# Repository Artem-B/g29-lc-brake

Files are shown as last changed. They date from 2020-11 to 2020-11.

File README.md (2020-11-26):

# Logitech G29 pedals mod
- [Logitech G29 pedals mod](#logitech-g29-pedals-mod)
  - [What it does](#what-it-does)
  - [Why](#why)
  - [Required hardware](#required-hardware)
  - [Software](#software)
  - [Hardware -- the real hardware this time.](#hardware----the-real-hardware-this-time)
- [Build instructions](#build-instructions)

## What it does

- Adds load cell as the brake pressure sensor.
  - replaces lower part of the spring housing with a 3D-printed one.
- Adds Adafruit ItsyBitsy M4 express to process load cell data and
  potentiomenter readings as an independent (from the wheel) HID joystick with
  16-bit values. Un-invert the values reported by pedals while we're at that.

## Why

Humans easily adapt to control car braking by applying **pressure**. Logitech
pedals use potentiomenters that read pedal displacement. Relationship between
the applied pressure and the displacemmment is controlled by the brake's spring
with a rubber block intended to make the relationship non-linear. Unfortunately,
it squeezes whe wide range of high pressure values at the end of the pedal
travel into a rather narrow range of the pedal movement which Logitech software then attempts to normalize into something more sensible.

It mostly works, but in practice I've found it rather hard to modulate the brake pressure precisely. One moment the car does not brake enough, then all of a sudden ABS goes nuts (or the car spins out). It just does not behave like a real car brake.

So, after eyeballing various higher-end pedals I've decided that I'm not *that*
interested in spending my toy budget on the ready-made gear. Instead, I've
figured that I can just mod the pedals using mostly off-the shelf components and
whatever I had at hand.

TL; DR; It worked surprisingly well. Eventually.

## Required hardware

- Logitech G29/G920 pedals. The mod may work with G27 or other similar Logitech
  models, but you may need to tweak the spring housing model to fit.

- $15 [Adafruit ItsyBitsy M4 Express](https://www.adafruit.com/product/3800)
  
  It's amazing how much stuff you can cram into $15 worth of hardware:
  - ATSAMD51 32-bit Cortex M4 core running at 120 MHz
   
    You get a real 32-bit ARM processor, with tons of peripherals and you can
    program it in Python, if you want to. Why anyone is still using AVR-based
    overpriced and underpowered Arduino boards these days is beyond me.
  - Floating point support with Cortex M4 DSP instructions. -- M4 can do *a lot*
    of signal processing, if needed.
  - 512 KB flash, 192 KB RAM -- should be enough for everyone, right?
  - 2 MB SPI FLASH chip for storing files and CircuitPython code storage.

  Another option is [Feather M4](https://www.adafruit.com/product/3857) ($23)
  which uses the same processor as the `ItsyBitsy M4`  and comes with some
  breadboard space which would be handy.

  You could also save few bucks and go for [QT
  Py](https://www.adafruit.com/product/4600) ($6),  [Trinket
  M0](https://www.adafruit.com/product/3500) ($9), or [ItsyBitsy
  M0](https://www.adafruit.com/product/3727) ($12). These boards use `Cortex-M0`
  and are slower than the `Cortex-M4` on the `ItsyBitsy M4`, but should still be
  more than sufficient to do the job.

  Other thoughts:

    About any chip with an USB interface, couple of GPIO pins for I2C and three
    ADC-capable inputs could do the job. `ItsyBitsy M4` is way overpowered for
    that and was largely chosen for convenience of writing software in Python.

    Surprisingly, not that many low-cost Cortex-M based boards have USB support.
    My usual go-to
    [`Discovery`](https://www.st.com/en/evaluation-tools/stm32-discovery-kits.html)
    and
    [`Nucleo`](https://www.st.com/en/evaluation-tools/stm32-nucleo-boards.html)
    boards from `STM` use USB for built-in STLink debugger and only pass through
    UART to the host.

    Trivia bit: $13 STM's
    [Nucleo-32](https://www.st.com/en/evaluation-tools/nucleo-g431kb.html) which
    is based on `stm32f431kb` uses `stm32f723` for the built-in ST-Link
    debugger. `F732` alone costs as much as the board and is much more capable
    than the `stm32f4` chip it debugs. How can one buy the whole board for less
    than the sum of the parts is a mystery to me. Can't complain though.

    ESP32 may be an interesting option for interfacing with the computer via
    Bluetooth, but that was considered to go beyond the `keep it simple`
    approach I was going for.

- $30 [FX29K0](https://www.te.com/usa-en/product-CAT-FSE0006.html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)
  100lbf/50kg load cell with I2C interface. 
  
  - Part number: FX29K0-100A-0100-L
  - [Datasheet](https://www.te.com/commerce/DocumentDelivery/DDEController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) for FX29 load cells.
  - [Datasheet](https://www.idt.com/us/en/document/dst/zsc31014-datasheet) for `zsc31014` which is the measurement controller inside the FX29 load cell.

  There are quite a few variants of the load cell. You need the one starting
  with `FX29K` or `FX29J`, and ending with `0100-L` pr `0500-N`. If you use
  `FX29K`/`FX29J` followed by a digit other than `0`, you will need to adjust
  the I2C address in the `code.py`.

  The cell costs about $30 and is available from the usual sources.
  - [Digikey](https://www.digikey.com/en/products/detail/te-connectivity-measurement-specialties/FX29K0-100A-0100-L/11205661)
  - [Mouser](https://www.mouser.com/ProductDetail/Measurement-Specialties/FX29K0-100A-0100-L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)
  - [Others, via octopart.com](https://octopart.com/search?q=FX29K0-100A-0100-L&currency=USD&specs=0)

- Female DB-9 connector.
  
  Used to read the stock potentiomenter values via the reguler DB-9 connector from the pedals that normally plugs into the wheel base.

  I've repurposed an old serial cable I had in my `junk that may be useful one day` bin.

## Software

- [CircuitPython](https://circuitpython.readthedocs.io/en/6.0.x/README.html)
  
  That turned out to be the easiest way to get things working. I've considered
  multiple alternatives, but this method ended up winning based on the `results
  delivered`/`annoyance caused` ratio.

  - My [repo with the modified CirquitPython](https://github.com/Artem-B/circuitpython)

    The only changes are to ass `PEDALS` USB HID device for `ItsyBitsy M4 Express` board. If you want to use a different board, you'll need to make similar changes for that board.

  - Pedals software (this repo)
    
    It's a simple python script that reads the values from `FX29` and the values
    of the stock potentiometers and reports them via USB. It also continually
    prints all the values over the serial port. It could be used to measure the
    relatinship between pedal displacement and the reported load. E.g. here is
    what my brake pedal reports depending on the spring setup: brake pedal load/displacement chart

    The result is roughly comparable to the much more expensive 
    [Heusinkveld Sim Pedals Ultimate](https://www.cranfieldsimulation.com/shop/sim-pedals-ultimate-heusinkveld/):
    

## Hardware -- the real hardware this time.

- Coins. I've used Euro 10c, [Danish 2
  kroner](https://en.wikipedia.org/wiki/Danish_krone) (yay for a center hole!)
  and an US 25c coins. You could probably use other coins, possibly filed down to
  size, or find appropriately sized washers.
- M4-0.7x20 screw + nut, but the size is not particularly critical, we just need
  a bump that will push on the load cell.

First mod version was prototyped using a bunch of schedule 40 PVC pipes and
couplers. It didn't quite work out. I had to build both upper and lower parts of
the spring housing. Making the parts telescoping into each other was hard to do
within the limited size choices and the constraints imposed by the pedal frame.
Without parts snugly fitting into each other, the spring buckles under the load
and the whole contraption flies apart. It turns out g29 pedal design uses a
number of subtle tricks to constrain spring housing motion to prevent spring
buckling. 

# Build instructions

See [Build.md](./Build.md) for the gory details.

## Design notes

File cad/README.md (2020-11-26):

# 3D-printable CAD model for the lower part of the spring housing.



This directory contains design file in `STEP` format and `STL` model for 3D printing.

You can poke at the model online:
- [Onshape](https://cad.onshape.com/documents/33ba29857d75f513ac8580a0/w/af6bbb602e60010e2369d8d1/e/88f17d0aba57d4f3874d157d).
- [Fusion360](https://a360.co/3l7wu99)

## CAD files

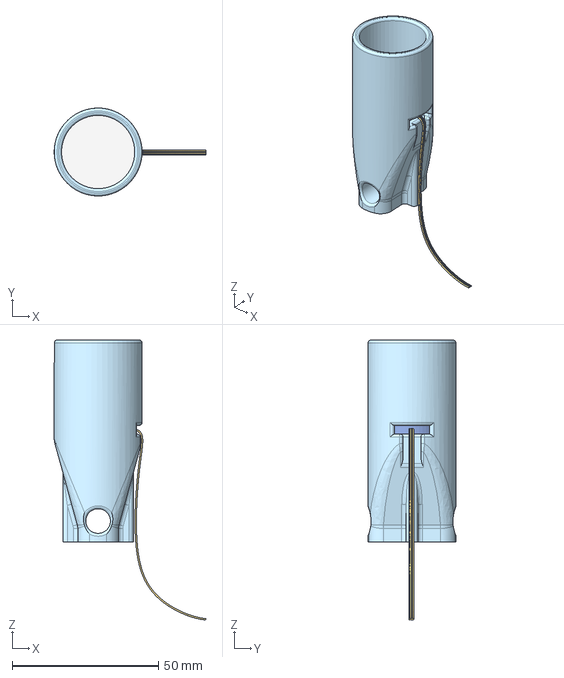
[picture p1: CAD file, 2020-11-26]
cad/g29 brake load cell mod.step
51.8 x 30.0 x 95.6 mm

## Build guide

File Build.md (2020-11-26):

# G29 brake mod build instructions.
- [G29 brake mod build instructions.](#g29-brake-mod-build-instructions)
  - [Software](#software)
    - [Build modified CircuitPython firmware](#build-modified-circuitpython-firmware)
    - [Update CircuitPython firmware](#update-circuitpython-firmware)
    - [Install required CircuitPython libraries](#install-required-circuitpython-libraries)
  - [Hardware](#hardware)
    - [Wiring](#wiring)
    - [3D print the spring holder](#3d-print-the-spring-holder)
    - [Assemble the mod](#assemble-the-mod)
    - [Mod the pedals.](#mod-the-pedals)
  - [Debugging](#debugging)

## Software

### Build modified CircuitPython firmware

Follow [CircuitPython build instructions](https://learn.adafruit.com/building-circuitpython/build-circuitpython) for `ItsyBitsy M4 Express`:

```shell
$ git clone https://github.com/Artem-B/circuitpython
$ cd circuitpython
$ git checkout main
$ git submodule sync --quiet --recursive
$ git submodule update --init
$ make -C mpy-cross
$ cd ports/atmel-samd
$ make BOARD=itsybitsy_m4_express
```

Once you're done you should have `build-itsybitsy_m4_express/firmware.uf2` file.

### Update CircuitPython firmware

Official Adafruit's [Firware upgrade instructions](https://learn.adafruit.com/introducing-adafruit-itsybitsy-m4/uf2-bootloader-details).

- double-click `reset` button on the ItsyBitsy board.
- you should see a new removable drive labeled `ITSYM4BOOT`
- copy `firmware.uf2` from the step above to that drive.

### Install required CircuitPython libraries

Once the firmware has been updated, you should see a new removable drive labeled
`CIRCUITPY`. That's where python files will go. 

- download the latest circuitpython library bundle from
  https://circuitpython.org/libraries and unpack it somewhere. Copy following
  files from the bundle into the `lib` directory on the `CIRCUITPY` drive:
  ```
  adafruit_hid/*
  simpleio.mpy
  ```
- copy all `.py` files from this repository into the root of the `CIRCUITPY` drive.

Software is ready to go now.

## Hardware

### Wiring

- I2C

    In order for I2C communication to work, you need to add two pull-up resistors -- one between `SCL` and `3.3V`, and one between `SDA` and `3.3V`.

- DB-9 for original pedal potentiomenters.

    Wire DB-9 Female connector pins to the following pins on `ItsyBitsy M4`:

    | DB-9 pin | `ItsyBitsy M4` pin | Purpose          |
    |----------|--------------------|------------------|
    |     1    | 3V                 | Reference voltage|
    |     2    | A0                 | Accelerometer pot|
    |     3    | A1                 | Brake pot        |
    |     4    | A2                 | Clutch pot       |
    |     6    | G                  | Signal Ground    |

- 4-pin connector for the load cell. 
  
  Wire connector pins for the load cell's signals:
    | load cell | `ItsyBitsy M4` pin |
    |-----------|--------------------|
    |  Red      | 3V. A5, if you want to change load cell parameters. |
    |  Yellow   | SCL                |
    |  White    | SDA                |
    |  Black    | G                  |

  I've used the standard 100mil header pins.

  The red wire supplies power to the load cell. In order to access the load
  cell's command mode, I2C command must be issued within 1.5-6ms of the cell power up. I've used a GPIO pin to supply the load cell's power. The cell's power consumption is below the 8mA that could be supplied by a GPIO pin on the `SAMD51G`. Powering the load cell from the 3.3V directly is fine for just reading the load cell measurements.

### 3D print the spring holder

3D print the model in [`CAD`](cad/README.md) subdirecory. I've printed it using
0.6mm nozzle and 0.4mm layer. You may need to file off the seams on the inside
and the outside of the printed part to ensure that the spring and the upper part
of the housing move smoothly.

### Assemble the mod

Attach the the washer to the bottom of the load cell using double-sided tape (it
must be about paper-thin, do not use thick foam tape) or some glue.

Thread the load cell cable through the hole in the side of the housing.

Place the load cell into the holder, with the load point bump facing upwards.

Drill a hole in a 25c coin, put a screw through it and fix it in position with a nut. The length of the screw should be short enough to fit under the white plastic cap in the original holder. Alternatively, you could place an appropriately sized stand-off on the screw and use that instead of the cap to guide/center the spring and serve as the support for the rubber insert, if you're planning to use one.

Place the coin & screw assembly into the housing, screw head down, so it contacts the load cell's center.

### Mod the pedals.

[Disassembly instructions](https://youtu.be/DxT2UOmHN-I?t=885) by `Sim Racing Garage` on YouTube.

- remove both parts of the spring housing.
- replace lower portion with the mod.
- Drill a hole in the upper part of the pedals' case and thread the load cell
  cable through.
- Drill two or four of holes on the back of the upper pedals shell and thread a
  zip-tie(s) through them. The zip ties will be used to mount the `ItsyBitsy M4`
  board.
- re-assemble the pedals.
- Connect the load call wires to the header you've soldered (or wire them to the
  `ItsyBitsy M4` directly)
- Plug in the original pedals connector to the female DB-9 you've wired above.
- Connect `ItsyBitsy M4` to the host via USB.

## Debugging

CircuitPython creates a virtual serial port. If/when something goes wrong, the normally-green LED on the `ItsyBitsy M4` will start flashing other colors. Connecting to the serial port will give you access to the Python REPL running on the board. When the mod app runs normally, it prints out every measured value for each of the potentiometers and for the load cell, so you can use it to verify that the pedals respond as intended.

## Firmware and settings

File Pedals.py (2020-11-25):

# The MIT License (MIT)
#
# Copyright (c) 2018 Dan Halbert for Adafruit Industries
#
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

"""
`adafruit_hid.gamepad.Gamepad`
====================================================
* Author(s): Dan Halbert
"""

import struct
import time

from adafruit_hid import find_device


class Pedals:
    """ """

    def __init__(self, devices):
        """Create a Gamepad object that will send USB gamepad HID reports.
        Devices can be a list of devices that includes a gamepad device or a gamepad device
        itself. A device is any object that implements ``send_report()``, ``usage_page`` and
        ``usage``.
        """
        self._device = find_device(devices, usage_page=0x1, usage=0x04)

        # Reuse this bytearray to send reports.
        # 4 reports, 2-byte each = 8 bytes.
        self._report = bytearray(8)

        # Remember the last report as well, so we can avoid sending
        # duplicate reports.
        self._last_report = bytearray(8)

        # Store settings separately before putting into report. Saves code
        # especially for buttons.
        self._joy_x = 0
        self._joy_y = 0
        self._joy_z = 0
        self._joy_w = 0

        # Send an initial report to test if HID device is ready.
        # If not, wait a bit and try once more.
        try:
            self.reset_all()
        except OSError:
            time.sleep(1)
            self.reset_all()

    def set(self, x=None, y=None, z=None, w=None):
        """Set and send the given joystick values.
        The joysticks will remain set with the given values until changed
        One joystick provides ``x`` and ``y`` values,
        and the other provides ``z`` and ``r_z`` (z rotation).
        Any values left as ``None`` will not be changed.
        All values must be in the range -127 to 127 inclusive.
        Examples::
            # Change x and y values only.
            gp.move_joysticks(x=100, y=-50)
            # Reset all joystick values to center position.
            gp.move_joysticks(0, 0, 0, 0)
        """
        if x is not None:
            self._joy_x = self._validate_value(x)
        if y is not None:
            self._joy_y = self._validate_value(y)
        if z is not None:
            self._joy_z = self._validate_value(z)
        if w is not None:
            self._joy_w = self._validate_value(w)
        self._send()

    def reset_all(self):
        """Release all buttons and set joysticks to zero."""
        self._joy_x = 0
        self._joy_y = 0
        self._joy_z = 0
        self._joy_w = 0
        self._send(always=True)

    def _send(self, always=False):
        """Send a report with all the existing settings.
        If ``always`` is ``False`` (the default), send only if there have been changes.
        """
        struct.pack_into(
            "<hhhh",
            self._report,
            0,
            self._joy_x,
            self._joy_y,
            self._joy_z,
            self._joy_w,
        )

        if always or self._last_report != self._report:
            self._device.send_report(self._report)
            # Remember what we sent, without allocating new storage.
            self._last_report[:] = self._report

    @staticmethod
    def _validate_value(value):
        if not -32768 <= value <= 32767:
            raise ValueError("Out of range")
        return value

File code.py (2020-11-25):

import board
import time
import simpleio
import usb_hid
import math
import digitalio
import analogio
from struct import pack_into, unpack
import Pedals

def f(x):
    return int(32760*math.sin(float(x)/1000.0))

pedals = Pedals.Pedals(usb_hid.devices)

def pedal_sim():
    t = 0;
    while True:
        print("t=", t)
        pedals.set(x=f(t), y=f(t*2), z=f(t*3), w=f(t*4))
        t = t+1
        time.sleep(0.01)

def scan_i2c():
    i2c = board.I2C()
    
    while not i2c.try_lock():
        pass
    
    try:
        while True:
            print("I2C addresses found:", [hex(device_address)
                for device_address in i2c.scan()])
            time.sleep(2)
    
    finally:  # unlock the i2c bus when ctrl-c'ing out of the loop
        i2c.unlock()    
        pass

class FX29:
    def __init__(self, addr=0x28, power_pin=board.A5):
        self._pwr = digitalio.DigitalInOut(power_pin)
        self._pwr.direction = digitalio.Direction.OUTPUT
        self.power(True)
        self._i2c = board.I2C()
        self._addr = addr
        self._buf = bytearray(4)
        self._i2c.unlock()
        while not self._i2c.try_lock():
            pass
        print("FX29 created")

    def power(self, on):
        self._pwr.value = on
        
    def read_mr(self):
        # Just read command & STOP
        self._i2c.readfrom_into(self._addr, self._buf, end = 0)

    @staticmethod
    def _sv(value):
        "Returns status/value tuple"
        s = value >> 14 & 0x3
        v = value & 0x3fff
        return s,v

    @staticmethod
    def _temp(value):
        "Returns temperature"
        t = value >> 5 & 0x3ff
        return t


    def read_mr2(self):
        # bridge data
        self._i2c.readfrom_into(self._addr, self._buf, end = 2)
        value, dummy = unpack('>HH', self._buf)
        s,v = self._sv(value)
        return s, v

    def read_mr4(self):
        # Bridge data & temperature
        self._i2c.readfrom_into(self._addr, self._buf)
        value, t = unpack('>HH', self._buf)
        s,v = self._sv(value)
        if s == 3:
            print("")
        return s, v, self._temp(t)


    def write_mr(self):
        # Write w/ no data
        self._i2c.writeto(self._addr, self._buf, end = 0)

    def enter_cmd_mode(self):
        self.power(False)
        time.sleep(0.01)
        self.power(True)
        time.sleep(0.003) # We have ~6 ms to enter command mode.
        self.cmd(0xA0)

    def exit_cmd_mode(self):
        self.cmd(0x80)
        time.sleep(0.02) # It may take up to 20ms to exit if we need to update EEPROM.
    
    def cmd(self, cmd, data=0):
        pack_into('>BHx', self._buf, 0, cmd, data)
        self._i2c.writeto(self._addr, self._buf, end=3)

    def read_eeprom(self, offset):
        if not 0 <= offset <= 0x13:
            return
        self.cmd(offset, 0)
        self._i2c.readfrom_into(self._addr, self._buf, end=3)
        ack, value = unpack('>BHx', self._buf)
        if ack != 0x5a:
            print("Got unexpected EEPROM read response:", hex(ack), hex(value))
            return
        return value

    def write_eeprom(self, offset, value):
        if not 0 <= offset <= 0x13:
            return
        v0 = self.read_eeprom(offset)
        # Write the new value
        self.cmd(0x40+offset, value)
        time.sleep(0.02) # EEPROM write takes up to 15ms
        v1 = self.read_eeprom(offset)
        print("W[%d]= %s:  %s -> %s" % (offset, hex(value), hex(v0), hex(v1)))

def adc_to_axis(v):
    return -32768 + (0xffff - v)

def load_to_axis(v):
    return int(-32768 + 3 * max(0, v-1000)) # Full span is 1000-15000, stretch it a bit.

def measure(fx29):
    accelerator_v = analogio.AnalogIn(board.A0)
    brake_v = analogio.AnalogIn(board.A1)
    clutch_v = analogio.AnalogIn(board.A2)
    last = time.monotonic_ns()
    last_report = last
    sent = 0
    t = 0
    while True:
        s, load = fx29.read_mr2()
        if s:
            continue
        brake = brake_v.value
        acc = accelerator_v.value
        clutch = clutch_v.value
        now = time.monotonic_ns()
        pedals.set(
            x=load_to_axis(load),
            y=adc_to_axis(brake),
            z=adc_to_axis(acc),
            w=adc_to_axis(clutch))
        sent += 1
        dt = (now - last ) // 1000
        last = now
        print(acc, brake, clutch, load, load_to_axis(load))
        last = now

def dump_eeprom(fx29):
    fx29.enter_cmd_mode()
    for i in range(0x13+1):
        v = fx29.read_eeprom(i)
        print(i, hex(v))
    fx29.exit_cmd_mode()

def disable_sleep(fx29):
    fx29.enter_cmd_mode()
    v = fx29.read_eeprom(1)
    if True or (v & 0x20):
        fx29.write_eeprom(1, 0x8001)
        v1 = fx29.read_eeprom(1)
        print("eeprom[1] : %s -> %s " % (hex(v), hex(v1)))
        fx29.exit_cmd_mode()
    fx29.exit_cmd_mode()


fx29 = FX29()
#dump_eeprom(fx29)
#disable_sleep(fx29)
#dump_eeprom(fx29)
#scan_i2c()
measure(fx29)
